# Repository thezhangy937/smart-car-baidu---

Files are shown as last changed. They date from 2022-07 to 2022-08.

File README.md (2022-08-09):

# smart-car-baidu---

飞思卡尔智能车17届完全模型组部分资料开源
由于我们组只是来玩智能车的，对奖项和速度没有太高的欲望
因此把时间精力花在了优化调车体验上面，现在进行一个简单的分享
希望对大家有所帮助，再接再厉，骚的飞起
-------------------------------------------------------------------------由于本人考研备考中，更新较慢，将就着看）

___

[TOC]

# 目录：

- edgeboard端网络连接优化
- 车壳3D建模
- 机械结构优化
- 单片机布局优化

---

## edgeboard端网络连接优化
  首先就是大家都头疼的一个问题,网卡的适配问题.
  我们队先后尝试过官方的无线网卡,网线连接,其他驱动移植等方法,效果都不太理想.
  在经历了两天,拖着三米长的网线跟着车跑的尴尬局面之后,本人忍无可忍,想到了一个非常天才的解决方法,最终实现效果好极了.

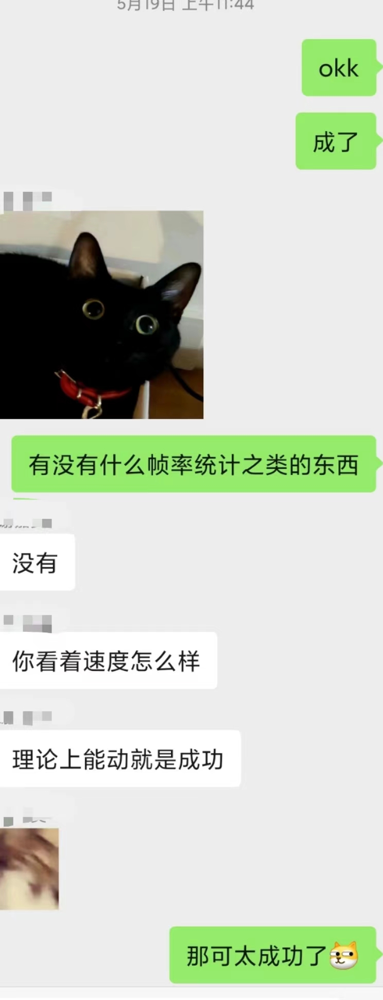
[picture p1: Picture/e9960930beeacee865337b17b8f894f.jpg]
<div align=center>
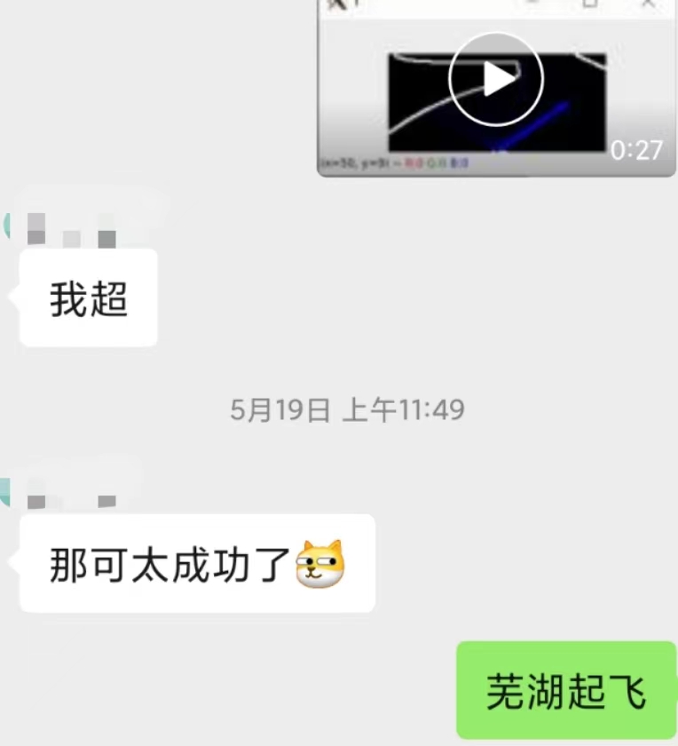
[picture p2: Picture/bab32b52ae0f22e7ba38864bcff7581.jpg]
<div align=center>

   实现的思路其实群里有老哥也已经发现了,既然网卡出错的原因是USB带宽不足,那干脆就不走USB口

   一开始本来是想用串口的,毕竟摄像头组别的无线图传也比较成熟了,无论是自己开发还是成品都可以买,但也有老哥提到edgeboard的串口也存在延迟,而且这个方案的上限太低了

   最后感谢万能的淘宝,找到了给摄像头监控用的无线网桥,原理是把rj45有线网的信号转成无线网络进行数据传输,从实现原理上达到了免驱,实际使用效果还行

   这里就不放链接了,毕竟我们当时时间宝贵,直接买了200+的5g版本,事实证明根本跑不了这么高的速度,理论上只要是无线网桥就行,大家备战18届的有充足的时间踩坑(๑*◡*๑)(好吧给土豪们留一个算了https://m.tb.cn/h.fyRJVZz?tk=CkEd2sIl2ku)

   最终的实现效果上,网络连接非常稳定,传输小的视频流没什么压力,命令行无延迟,基本实现了所有的需求.

---

## 车壳3D建模

	开源一部分车壳的建模,仅供大家标定尺寸,放在moddle目录下,<font color="blue">无法直接3D打印,必须修改</font>,希望大家充分发挥自己的创意
<font color="red">下图中红框的四个孔位以及蓝圈中的轮胎开孔已经打印测试,误差在可以接受的范围内,其他部分请针对自己的机械结构自行修改</font>

 <font color="red">下图中红框的四个孔位以及蓝圈中的轮胎开孔已经打印测试,误差在可以接受的范围内,其他部分请针对自己的机械结构自行修改</font>

 <font color="red">下图中红框的四个孔位以及蓝圈中的轮胎开孔已经打印测试,误差在可以接受的范围内,其他部分请针对自己的机械结构自行修改</font>

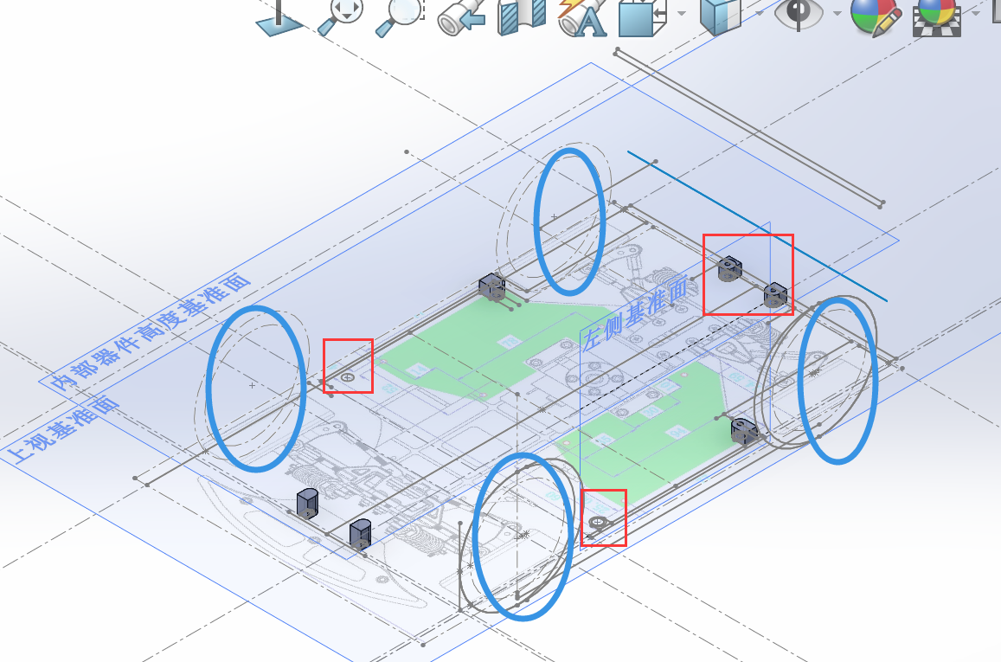
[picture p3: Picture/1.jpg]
<div align=center>

	基准面说明:
	上视基准面为底面
	左视基准面为外壳左面靠内侧
	内部器件高度基准面为官方edgeboard摆放的高度,引擎盖部分需要比这个高

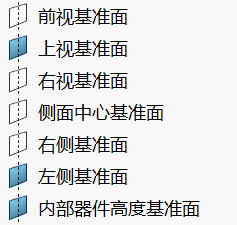
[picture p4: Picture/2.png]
<div align=center>

	建模注意事项:
	如果不打算预留防撞板的话,车壳最前端到舵机的高度变化非常距离,需要处理好
	由于此车模前轮打角范围很大,建模时一定要留出足够大的空间,大致像下图画的轮廓做一个切割
	摄像头开孔建议自行设计方便拆卸
	底部固定孔位建议花点心思弄成金属孔位,否则多次拆卸会造成孔位松动难以固定
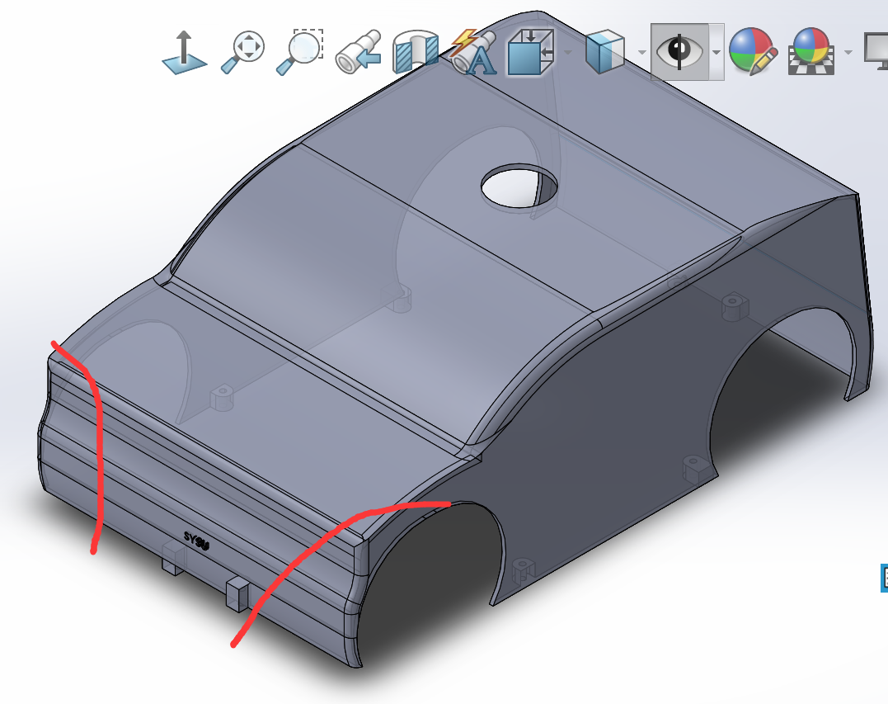
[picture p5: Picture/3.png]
<div align=center>

---

## 机械结构优化

### I车模的特点
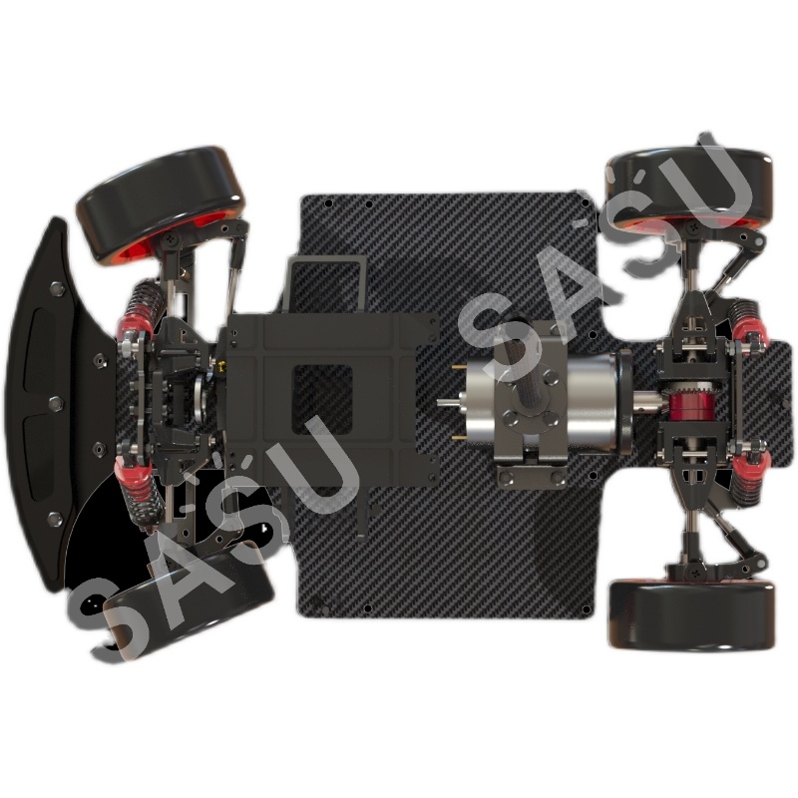
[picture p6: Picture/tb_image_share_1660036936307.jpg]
<div align=center>

1. 电机在中间,对布局有非常大的影响,两侧的宽度基本上只能放进去TC264核心板

2. 对外围器件的硬性要求很低,由于外壳的存在,屏幕可以不设计,走线简化了很多;单驱单编码器外加一个舵机以及串口,就可以达到完成任务的最低要求

3. 如果想像传统组别一样主驱分离,那主板跟驱动板基本上只能放在电机的两侧,再考虑到edgeboard的供电以及空间占用,以及电池到驱动板,驱动板到主板以及edgeboard之间都需要走大电流,走线上很难做到美观.

---

### 初代布局方案

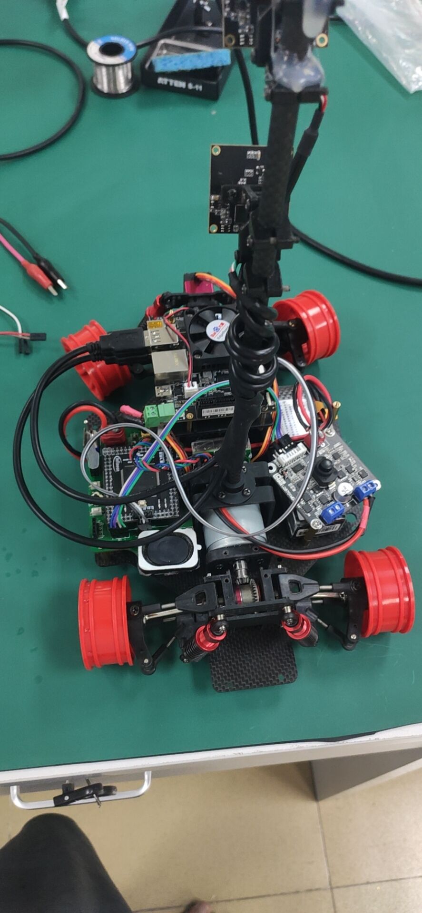
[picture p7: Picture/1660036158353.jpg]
<div align=center>

    可以看到:

- 线路杂乱,且电源线无法避免,驱动分离的设计引入了两根电机线加上两根电源线以及至少三根驱动控制线
- 没有位置抓车,不方便日常调车,特别是这辆车还很重的情况下
- edgeboard的位置和方向导致摄像头等USB排线会超出外壳的范围,导致必须使用拓展坞,这又会占用我们宝贵的空间
- edgeboard默认的支架位置实际上压缩了我们主控板的可用空间,进一步加大了画板难度,实际上这里已经把原来电池支架的位置锯掉然后将电池放在右侧,以增大主控板的可用面积

---

### 本人的布局思路

#### 布局设计

	首先,本人的目标是留出右侧一部分的空余空间用于拿车,然后尽可能给主控板留出足够大的空间,最后自行设计edgeboard的支架以及朝向,解决线路突出外壳的问题,而所有的这一切的主要难点就在解决固定孔位与电机位置的协调上

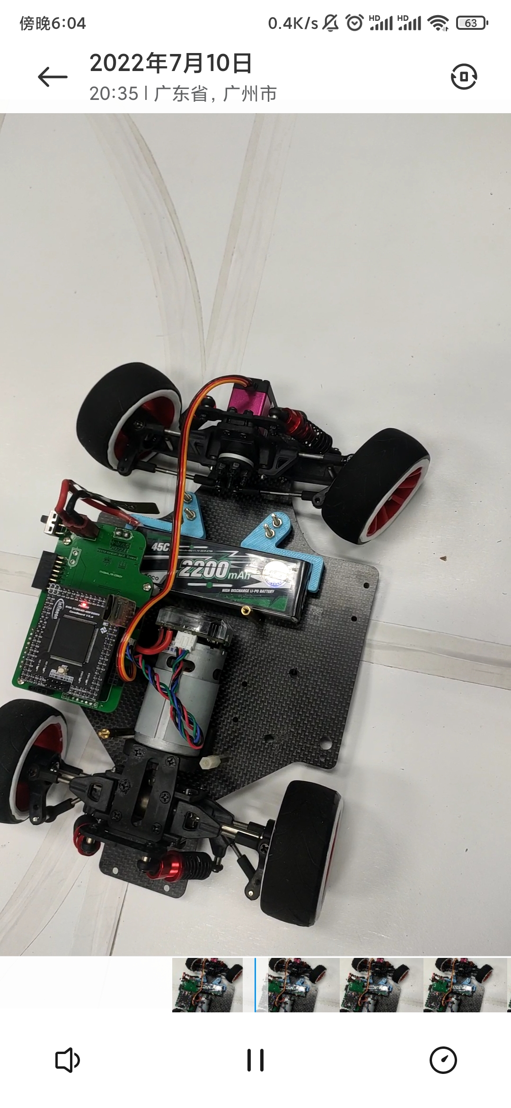
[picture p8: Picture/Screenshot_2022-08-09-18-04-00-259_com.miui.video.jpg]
<div align=center>

 上图就是本人设计的简易电池支架,有3D打印机的话20分钟就能设计并且打印出来,一共四个固定孔位,其中下面两个是底板自带的,上面两个是随便用电钻钻出来的.
  之所以设计成左右两个,一是因为电钻打出来有误差,不怎么对称,二是为了更好的固定电池,如下图,水平方向上电池已经被固定的很好,拆卸是只需要把电池往上扣即可,但由于安装车壳时还需要保证翻过来电池也不会掉,故采取了一点骚操作,仔细观察就可以发现,电池的正负极两根大粗线的中间是卡进支架的,利用这个设计就可以保证翻转时电池不掉落.拆卸电池时只需要拔掉板子上的端口即可抠出来.

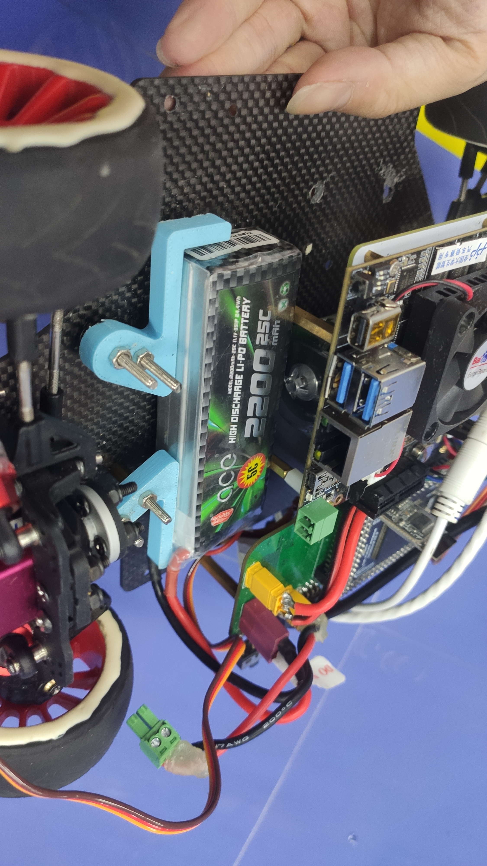
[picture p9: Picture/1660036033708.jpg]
<div align=center>

  解决了电池之后edgeboard支架便只剩下悬空edgeboard一个功能,因此本人调整了一下方向之后把位置往右稍微挪动了一点,并且把摄像头的固定孔位与其一起画到了PCB上面,如下图,此电路板最大的好处就是,布局的权限已经**==完全开放==**

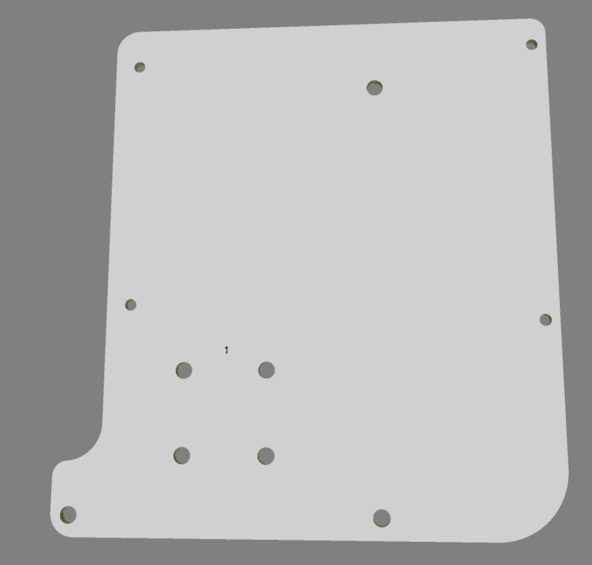
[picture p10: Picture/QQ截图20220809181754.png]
  <div align=center>

用户可以自己决定edgeboard的位置,也就可以随意决定主控板的大小,**==完全不需要担心被edgeboard支架以及摄像头支架限制==**

<div align=center>

最终的实现效果如图所示

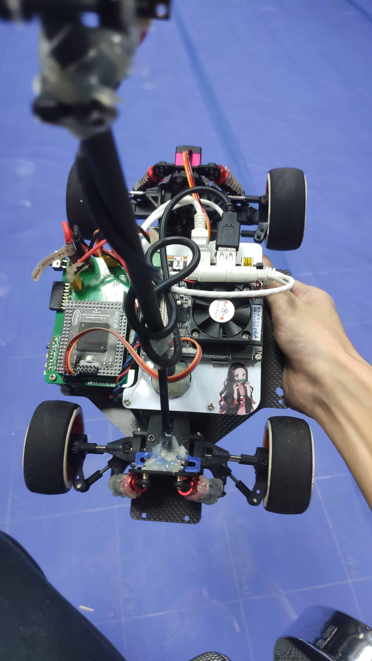
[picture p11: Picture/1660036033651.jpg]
<div align=center>

再把之前提到的网卡加上,位置也是刚刚好卡死,非常nice

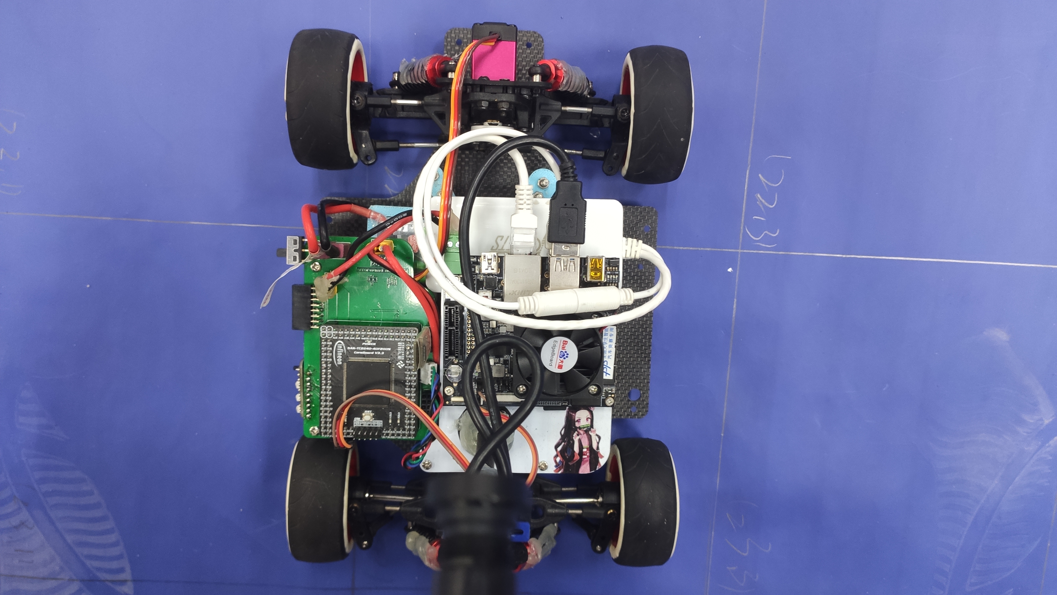
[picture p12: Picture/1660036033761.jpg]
<div align=center>
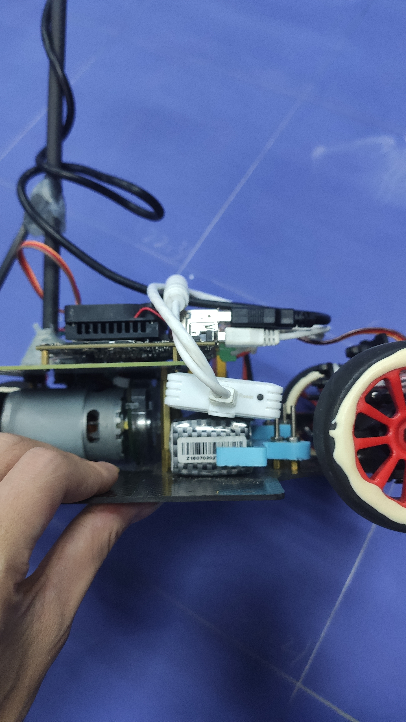
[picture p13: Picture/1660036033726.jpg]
<div align=center>

#### 单板集成
	反正立创开放了四层乃至六层板免费的打样服务,使用一块板子集成主控,电源转换以及驱动的功能,优点是大幅度减少了各种线,达到了强迫症勉强接受的程度,只剩下电池线,电机线,edgeboard供电线等无法减少的接线.

	缺点就是这个组别的煞笔舵机经常烧,不设计限流的话很容易焊板子焊到不省人事,没有主驱分离来的保险

---

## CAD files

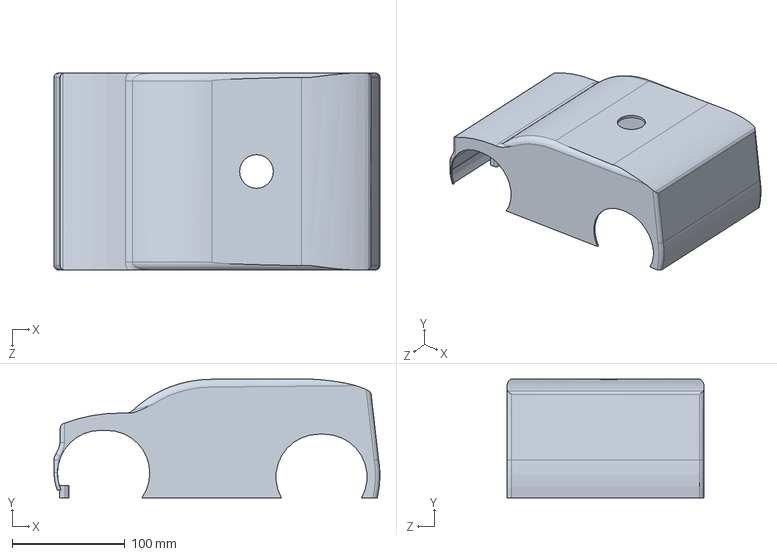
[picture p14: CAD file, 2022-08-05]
Moddle/打印版本改.SLDPRT
289.8 x 105.8 x 175.0 mm

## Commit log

2022-08-04 Create SolidWorks外壳
2022-08-05 一波小更新
    [打印版本改.SLDPRT]
